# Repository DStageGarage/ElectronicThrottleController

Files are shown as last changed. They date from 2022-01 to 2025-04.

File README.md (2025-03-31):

# ElectronicThrottleController

IMPORTANT - For production in JLCPCB please use v1.3 or v2.2 files! 

This is a project of Electronic Throttle Controller also known as Drive By Wire, created by Filip from DStage garage and free to use.

## HW generation 1
> [!IMPORTANT]
> ETC v1.3 is only suited for potentiometer based throttle position sensors and gas pedals as it uses a simple calibration method.
> 
The board is purely analogue, no programming required and no chance of failure due to MCU hang-up, flash disappearing due to harsh engine environment etc. Safety was a priority with this one ;-) It also has build in simple fail safes - in case any of the control wires is broken or shorted with power for example the throttle will close automatically.

The board shape is designed to fit popular aluminium casing to be found in tme.eu, Farnell etc. You can also use the provided STL file for 3D printing the case.There are no connectors, wires are soldered directly to the board to keep it compact.

You can also check a video to learn more about this project: https://www.youtube.com/watch?v=MTnsbOgZkUA 

## HW generation 2
> [!TIP]
> ETC v2.2 is suited for all types of throttle position sensors and gas pedals as it uses a different calibration method in comparison to v1.3.

The main functionality is purely analogue. If no special functions are desired the provided place for an optional Arduino Nano may stay unpopulated, no actions are required and the board will work in the same way as generation 1. The optional module can be used to monitor sensors but also to create a gas pedal map if required (basic SW in beta version is provided). All signals connected to the Arduino are buffered to minimise the risk in case of program failure. The usage of the Arduino module for throttle control has to be delibatery selected by desoldering jumper Z1 and soldering Z2. 

Wires can be soldered directly to the board, but this version allows you to use ARK terminals (screw terminals) instead. If PCB and assembly is ordered in JLCPCB user can chose BOM file with or without ARK terminals.
Besides the different input circuitry/calibration method compared to generation 1 this one is improved and better optimised in terms of heat dissipation.

The board form factor is larger than for version 1, but it will fit a popular aluminium casing, and a STL file for 3D printing is also provided. 

Here's a quick video comparing v2.2 with v1.3 https://studio.youtube.com/video/byb1L_GXVq8/edit

# Disclaimer: 
This device is dedicated for stationary engines and vehicles driving on private closed
properties. It should not be used on public roads!

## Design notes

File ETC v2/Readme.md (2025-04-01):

# ETC v2.x - 2nd HW generation

## Hisotry of changes
Last update 2024.11.13:
> [!IMPORTANT]
> A new recomended "low gain" BOM added.
> There is a known problem with some of the throttles where they tend to "flap" at some positions or when position is changed. This is most likely caused by the high gain of the error aplifier in PWM controller. In simple terms the PWM changes very fast so the throttle motor can not keep up thus starts oscilating.
> There are documented cases where lowering the gain  solves that issue. This new BOM changes value of R7 from 10k to 1k and R8 from 1k to 2.2k, efectively changing the ęrror amplifier gain from ~10 to ~0.45. This has not been tested with a "model" Bosch throttle yet but shouldn't cause any issues.

2023.10.04:
- beta SW for Arduino Nano and PC added, not tested

2023.08.30:
- two variants of 3D models fo case added

2023.08.22:
- Alternative BOM file version for v2.2 inclused screw terminal connectors so you can order them soldered in via JLCPCB
  
## Connection
| Connector | Signal | Function |
| :---: | :---: | :--- |
| P1 | GP | Gas pedal position signal. Most cases there are two redundand outputs from the gas pedal, use one on which voltage increases with pushing the pedal further. If both outputs have inclinig signal the one with wider voltage range is usually preferable. |
| P1 | GND | Use this pin for both gas pedal and TPS ground (negative power terminal). In case of potentiometer based sensors connect it to the low side of the potentiometer. |
| P2 | +5V | Use this pin for both gas pedal and TPS power (positive power terminal). In case of potentiometer based sensors connect it to the high side of the potentiometer. |
| P2 | TH | Throttle Position Sensor signal. Most cases there are two redundand outputs from the TPS, use one on which voltage increases with openning the throttle further. If both outputs have inclinig signal the one with wider voltage range is usually preferable. |
| P3 | GND | Use this pin for connecting to ECU signal ground when using IAC input and/or sharing the TPS signal. |
| P3 | IAC | Idle air PWM signal input from the ECU. In cas ECU has an open-collector/open-drain style IAC output (only connects to ground) user has to add pull-up resistor (for example 10k) to +5V on this input. Preferably the PWM signal should be 0-5V but 0-12V will also work. Please note that IAC has relatively high range by default and can open the throttle up to 30%. R26 can be increased in value to tighten the range and improve control resolution. |
| P4 | PWR | Main power terminal. Connect to +12V with a 5A fuse and a minimum of 1mm2 wire. |
| P4 | GND | Power ground for the board. Connect to a power ground on the vehicle with a minimum 1mm2 wire. |
| P5 | M1 | Throttle motor terminal 1. Polarity has to be checked experimentaly. |
| P5 | M2 | Throttle motor terminal 2. Polarity has to be checked experimentaly. |

## Calibration
Please refer to the DStage_ETC_v2.2_calibration.xlsx spreadsheet for calibration instructions.

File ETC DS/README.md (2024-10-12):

# DStage ETC DS
The "DS" stands for DSpeed as this version of ETC is dedicated for the Speeduino ECU by DStage called DSpeed: https://github.com/DStageGarage/DSpeed
It is based on HW version 2 howere it lacks the optional Arduino Nano module - as it is installed directly in the ECU some users can connect directly to ECU pins to creat gas pedal map if desired.

> [!IMPORTANT]
> Please note that this is a new project and has not yet been tested. It contains some crucial changes over ETCv2 such as the H-brdgethe being an integrated circuit intead of individual components. ALso the Layout is significantly different. Therefore there's no way of telling if it will behave as expected at the moment.

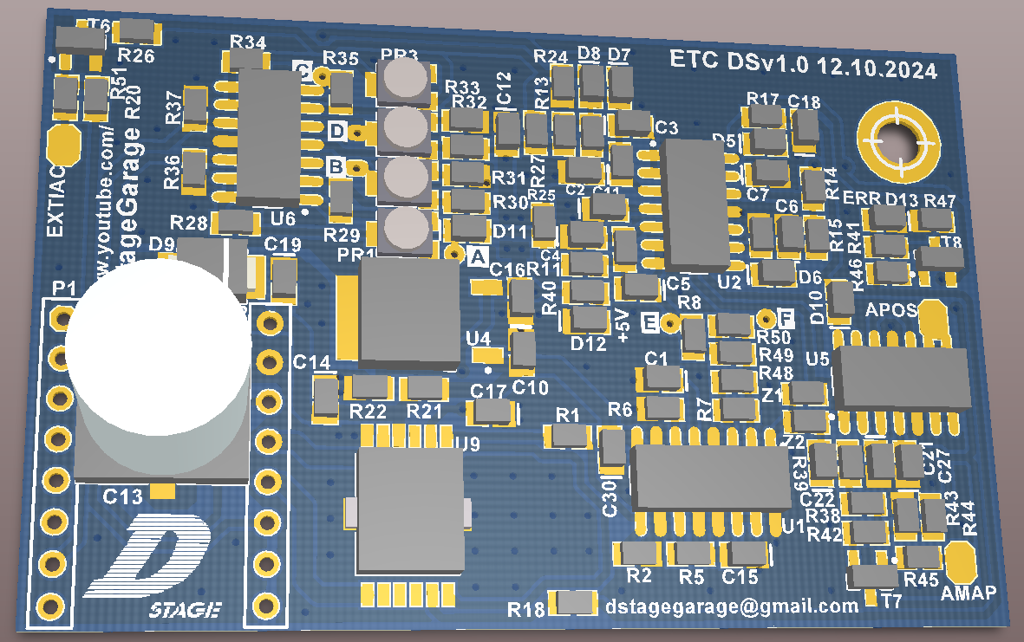
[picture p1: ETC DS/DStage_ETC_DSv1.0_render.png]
Render


For calibration instructions please use same sheet as for DSTage_ETCv2.2 - [DStage_ETC_v2.2_calibration.xlsx](https://github.com/DStageGarage/ElectronicThrottleController/blob/main/ETC%20v2/v2.2/DStage_ETC_v2.2_calibration.xlsx).

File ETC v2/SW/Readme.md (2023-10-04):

# SW for ETC v2.x

ETC v2.x allows for an optional Arduino Nano module. You will find the firmware for Arduino in "Arduino" folder and the aplication for controling it via PC in the "PC app" folder. 

Last update 2023.10.04:
- First beta version of both FW and app added. Please note that saving gas pedal map to a file as well as loading from a file is not yet available. Reading settings from Arduino to PC is slow and may be unstable when read multiple times so please pay attention if data makes sense. SW was not fully tested in real life conditions. Using Arduino functionality requires removing Z1 and adding Z2 jumper on the PCB. At the moment the Arduino code is fixed for "2000 RPM" which means it won't differentiate the map between RPMs and it's best to keep all columns in tyhe pam the same and set one of them to 2000 RPM. This can be easily incommented in the code and RPM signal can be used. For that user has to provide RPM signal from ECU to pin D3 of the Arduino Nano module - there is an extra pad on the v2.2 PCB next to that pin but no ARK connector. Signal cannot exceed 5V!

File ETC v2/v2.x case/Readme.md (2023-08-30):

# 3D model for ETC v2.x case

## DStage ETC basic case
Here you can find the basic project of 3d printable case for ETC v2.x PCB in Fusion 360 format.

There are also a ready to use stl models. Please note that the basic models do not contain holes for wires so user has to chose location for those and drill them manually. 
Models including wholes and mounting tabs will be added in future.

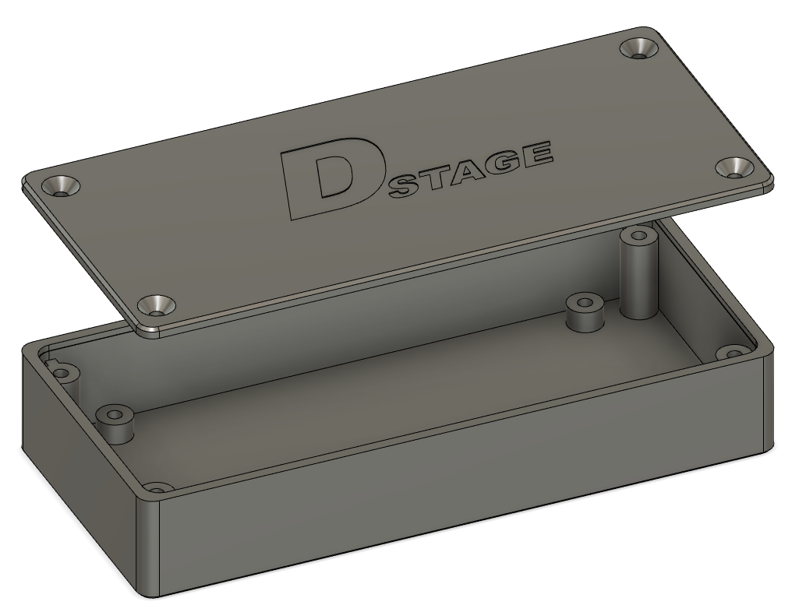
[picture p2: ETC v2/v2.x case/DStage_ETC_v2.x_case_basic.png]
Basic model for ETC v2.x without holes and tabs


## Alternative case by RSMtuning
Another approach to the case designed by one of the users - RSMtuning. This one does not use short bolts for PCB holding but a build in plastic spacer.

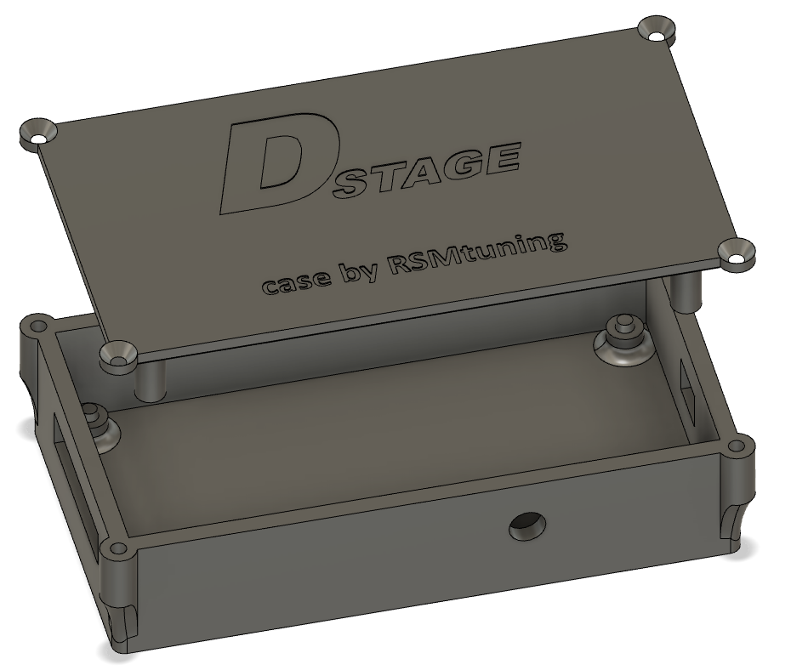
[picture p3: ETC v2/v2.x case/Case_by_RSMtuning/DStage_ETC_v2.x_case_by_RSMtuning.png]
Model for ETC v2.x by RSMtuning


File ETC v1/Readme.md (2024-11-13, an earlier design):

# ETC v1.x is the first HW generation 

2024.11.13:
> [!IMPORTANT]
> A new recomended "low gain" BOM added.
> There is a known problem with some of the throttles where they tend to "flap" at some positions or when position is changed. This is most likely caused by the high gain of the error aplifier in PWM controller. In simple terms the PWM changes very fast so the throttle motor can not keep up thus starts oscilating.
> There are documented cases where lowering the gain  solves that issue. This new BOM changes value of R7 from 10k to 1k and R8 from 1k to 2.2k, efectively changing the ęrror amplifier gain from ~10 to ~0.45. This has not been tested with a "model" Bosch throttle yet but shouldn't cause any issues.

2023.09.06:
- added 3D model for printing a case for v1.x

2023.03.26:
- v1.3 - changed the frequency of TPS input filter from 150Hz to 720Hz to avoid problem of tgrottle "flapping" due to too slow response presumably. 
  The new value has been tested on the bench and seems to solve the issue. No needto remove C2 and C3 now. 
  Changed component values: R9 from 5k1 to 10k, C2 from 100n to 22n, C3 from 220n to 22n.
- v1.3 - changed throttle motor PWM frequency from quite high ~300kHz to resonable ~100kHz. This change vastly reduces heat loss in H-bridge MOSFET transistors.
  As the dead time is achieved by difference in time of openning and closing the transistors (open by resistor, close by diode) majority of heat loses
  comes from channel opening time. With reduced frequency transistors are now much cooler.
- v1.3 - updated schematic in user manual and added note that there may be small differences in the looks of JLCPCB component list due to above changes in BOM.

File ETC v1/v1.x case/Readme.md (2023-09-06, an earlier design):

# 3D model for ETC v1.x case

Here you can find the basic project of 3d printable case for ETC v1.x PCB in Fusion 360 format.

There are also a ready to use stl models. Please note that the basic models do not contain holes for wires so user has to chose location for those and drill them manually. 
Models including wholes and mounting tabs may be added in future.

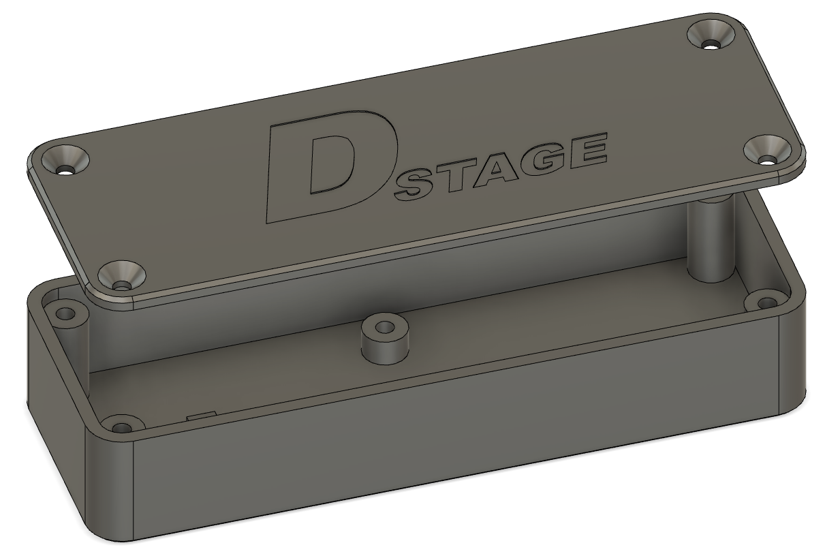
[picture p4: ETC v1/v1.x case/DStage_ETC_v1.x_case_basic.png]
Basic model for ETC v1.x without holes and tabs


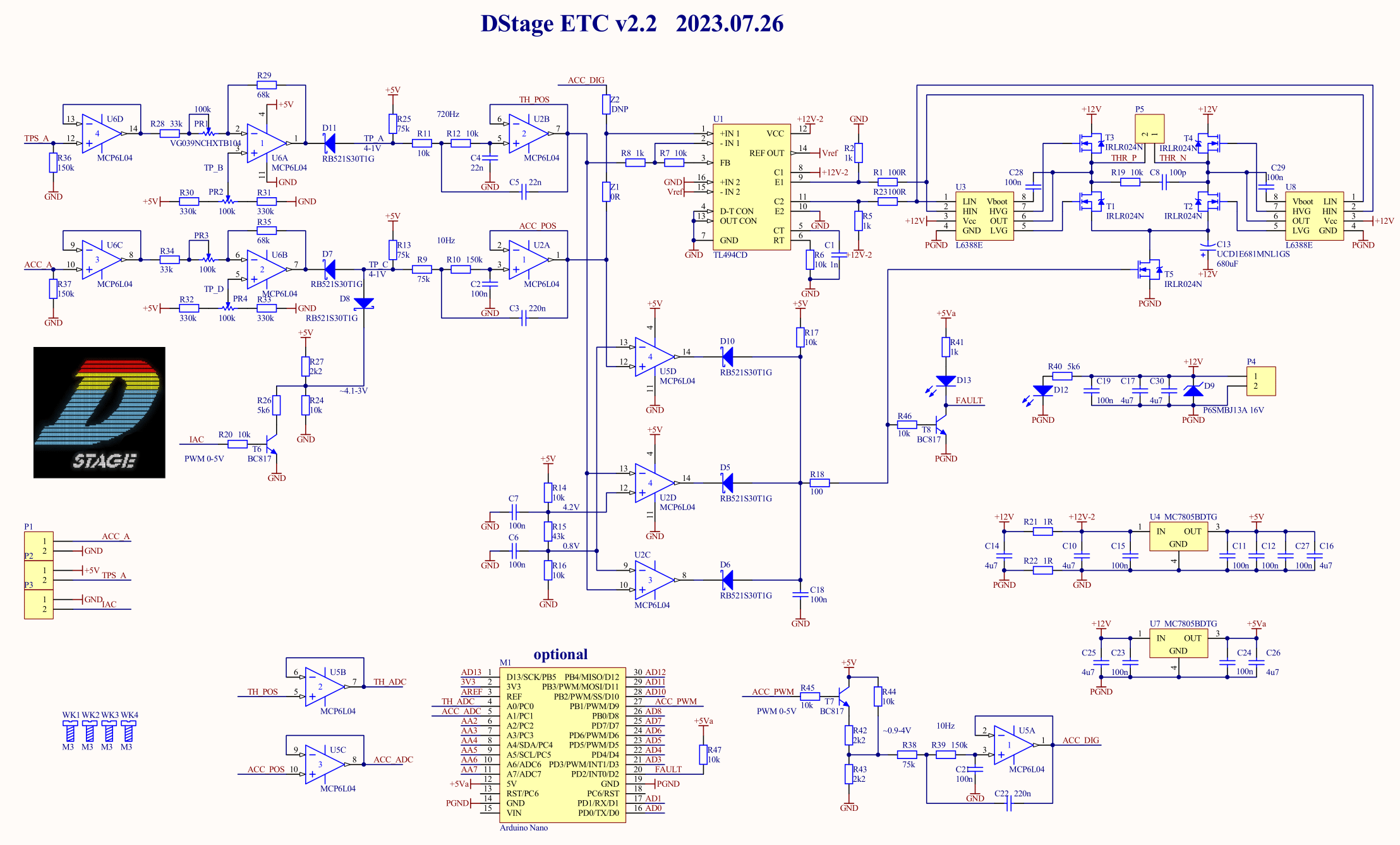
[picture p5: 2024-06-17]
ETC v2/v2.2/DStage_ETC_v2.2_schematic.png

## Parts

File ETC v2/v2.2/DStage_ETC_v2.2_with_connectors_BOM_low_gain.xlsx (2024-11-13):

Comment | Designator | Footprint | JLCPCB part #
RB521S30T1G | D5-8,D10-11 | 0805 | C167133
P6SMBJ13A | D9 | SMB | C86366
LED GREEN | D12 | 0805 | C2297 | basic
LED RED | D13 | 0805 | C84256 | basic
IRLR024N | T1-5 | D-Pak | C3007
S8050 | T6-8 | SOT-23 | C2146 | basic
TL494CD | U1 | SO16 | C19882 | extd
MCP6L04 | U2,U5-6 | SO14 | C116668
L6388E | U3,U8 | SO8 | C23921 | extd
MC7805BDTG | U4,U7 | D-Pak | C83632 | extd
100Ω | R1,R18,R23 | R0805 | C17408 | basic
1kΩ | R2,R5,R41 | R0805 | C17513 | basic
5.6k | R40,R26 | R0805 | C4382 | basic
10k | R6,R8,R11-12,R14,R16-17,R19-20,R24,R44-47 | R0805 | C17414 | basic
75k | R9,R13,R25,R38 | R0805 | C17819 | basic
150k | R10,R36-37,R39 | R0805 | C17470 | basic
330k | R30-33 | R0805 | C17629 | basic
43k | R15 | R0805 | C17695 | basic
1R | R21-22 | R0805 | C25271 | basic
2.2k | R7,R27,R42-43 | R0805 | C17520 | basic
68k | R29,R35 | R0805 | C17801 | basic
33k | R28,R34 | R0805 | C17633
100k | PR1-4 | SMD-3_3.0x3.8x1.2 | C128545 | extd
0Ω | Z1 | R0805 | C17477 | basic
1nF | C1 | C0805 | C46653 | basic
100nF | C2,C6-7,C11-12,C15,C18-19,C21,C23-24,C27-29 | C0805 | C28233 | basic
220nF | C3,C22 | C0805 | C5378 | basic
100pF | C8 | C0805 | C1790 | basic
270uF | C13 | SMD-ECAP-10x10 | C311670 | extd
4.7uF | C10,C14,C16-17,C25-26,C30 | C0805 | C1779 | basic
22nF | C4-5 | C0805 | C1729
screw terminal | P1-5 | 5mm | C474881 | extd

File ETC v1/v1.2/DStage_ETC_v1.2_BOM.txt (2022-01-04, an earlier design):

BOM for ETC project is shared via Google Drive for ease of use in Google spreadsheets. 

# Please follow this link: 
https://docs.google.com/spreadsheets/d/1jGTcMW5XZCuBMflX-EJ1iahN-_moxMeDLij978g0fmc/edit?usp=sharing 

The sheet inlused details regarding all components and their replacement as well as a tab with format dedicated for automatic assembly in JLCPCB.

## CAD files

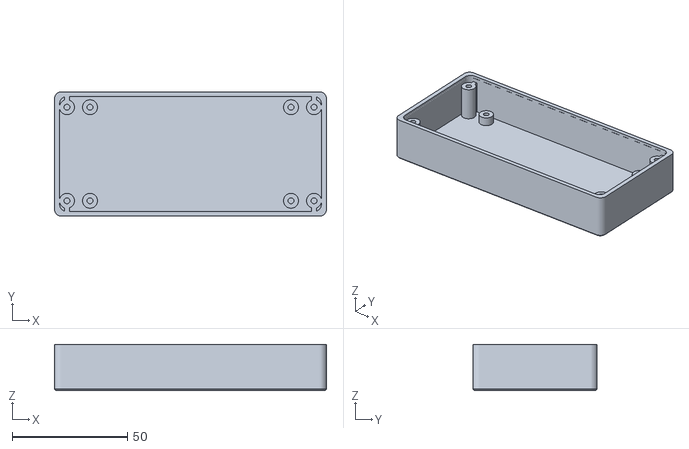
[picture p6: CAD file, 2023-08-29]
ETC v2/v2.x case/DStage ETC v2.x case main no holes.stl
118.0 x 54.0 x 20.0

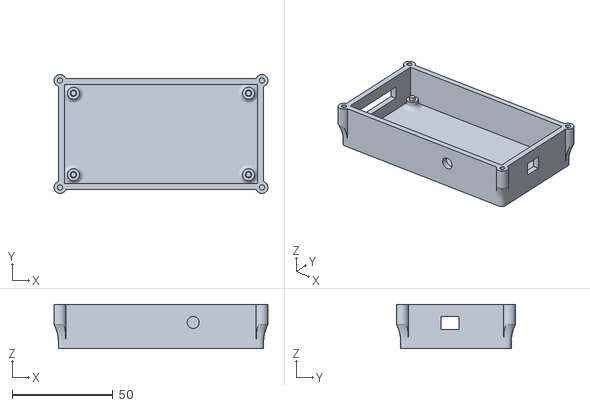
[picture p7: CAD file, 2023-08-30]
ETC v2/v2.x case/Case_by_RSMtuning/DStage_ETC_v2.x_case_by_RSMtuning_main.stl
106.3 x 59.1 x 22.0

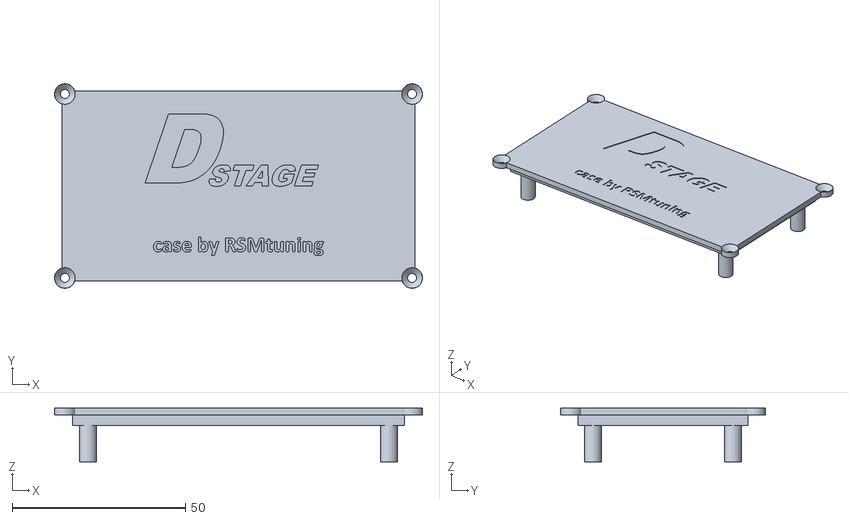
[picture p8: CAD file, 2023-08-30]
ETC v2/v2.x case/Case_by_RSMtuning/DStage_ETC_v2.x_case_by_RSMtuning_lid.stl
106.3 x 59.1 x 15.5

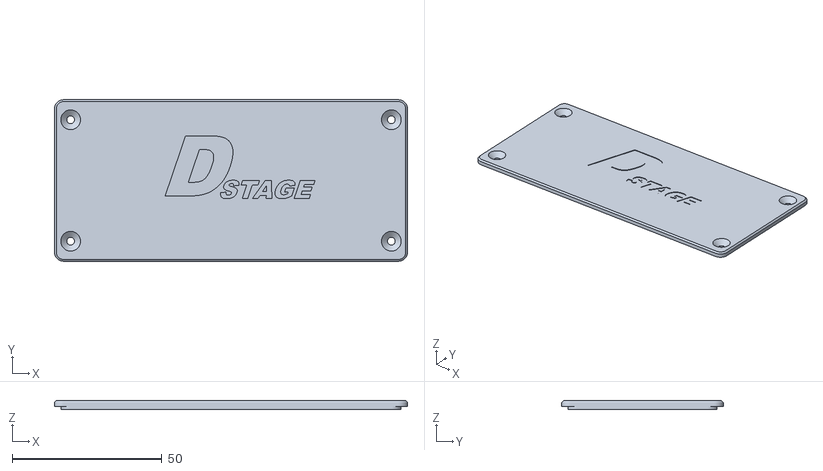
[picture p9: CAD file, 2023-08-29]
ETC v2/v2.x case/DStage ETC v2.x case lid no holes.stl
118.0 x 54.0 x 3.00

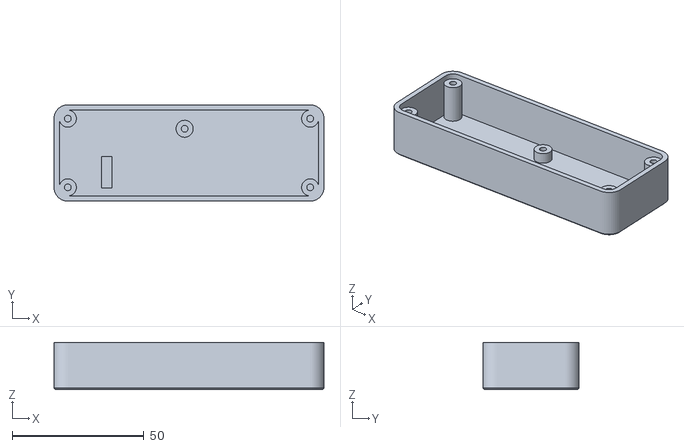
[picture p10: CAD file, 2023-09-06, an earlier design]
ETC v1/v1.x case/DStage ETC v1.x case main no holes.stl
102.5 x 36.6 x 18.0

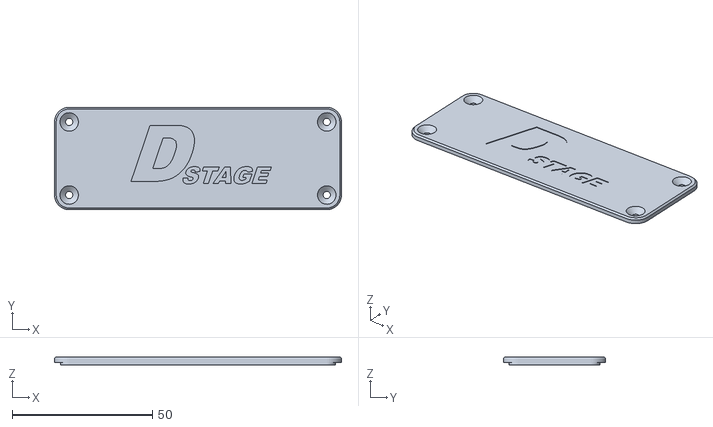
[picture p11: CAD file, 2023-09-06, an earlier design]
ETC v1/v1.x case/DStage ETC v1.x case lid no holes.stl
102.5 x 36.6 x 3.00

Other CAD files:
ETC v1/v1.x case/DStage ETC v1.x case basic project.f3d
ETC v2/v2.x case/Case_by_RSMtuning/DStage_ETC_v2.x_case_by_RSMtuning.f3d
ETC v2/v2.x case/DStage ETC v2.x case basic project.f3d

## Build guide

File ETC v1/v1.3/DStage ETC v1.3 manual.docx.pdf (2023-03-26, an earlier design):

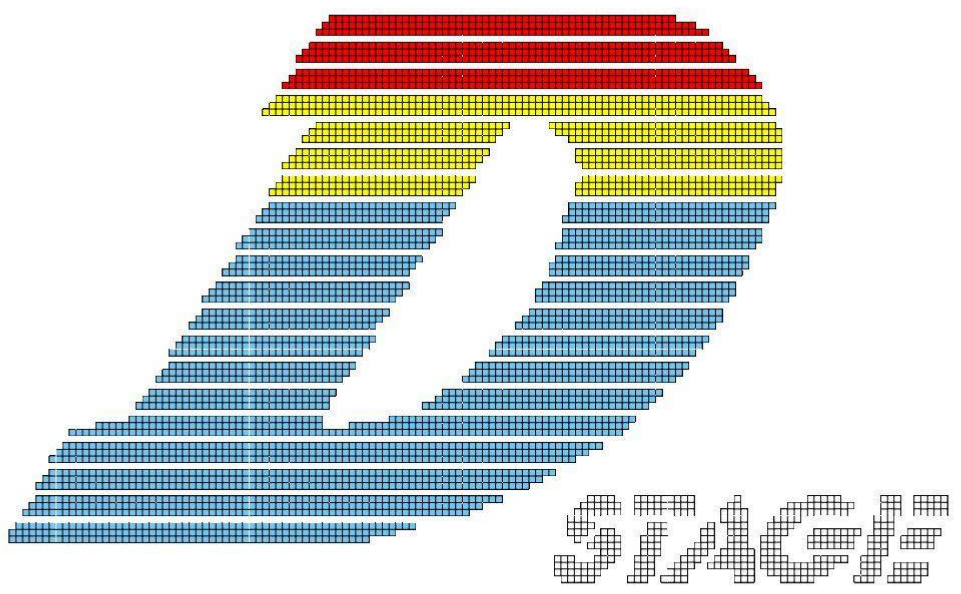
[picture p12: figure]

# Electronic Throttle Controller

a.k.a.

# Drive by Wire

# ETC v1.3

1

1. Introduction

The ETC v1.3 is an open project of a controller for electronic throttle for internal combustion engines. It allows control of the throttle by electronic gas pedal (accelerator) which is sometimes referred to as „drive by wire”. These are some of the features:
- Controls a DC motor based electronic throttle with H-bridge allowing for fast movement in both directions and closing the throttle beyond stationary position,
- Works with gas pedal incorporating potentiometers or voltage based output, highly adjustable input levels,
- IAC input allowing for ECU idle control with 5V PWM signal,
- Build in fail-safes for detecting broken connections or short circuits on wires connecting gas pedal and TPS,
- analogue circuit – no programming required, no risk of program failure, no risk of CPU going into race condition or resetting due to electromagnetic noise in hursh near-engine environment,
- PCB designed for enhancing immunity to noise.

DISCLAIMER:
This device is dedicated for stationary engines and vehicles driving on private closed properties. It should not be used on public roads!
2. Principle of operation

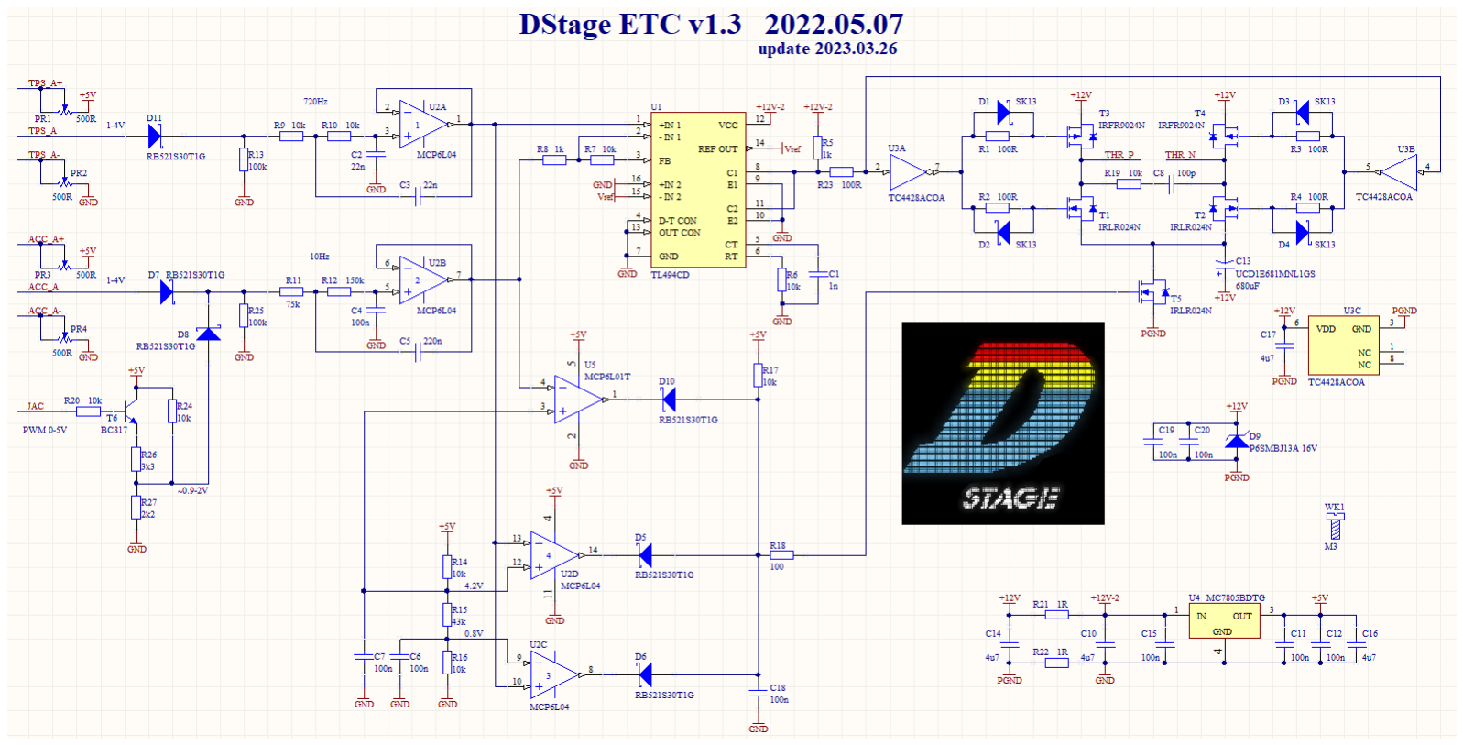
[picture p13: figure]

T.B.D.

2 Last update 2023.03.26

3. Assembly / Ordering

3.1 Automated assembly via JLCPCB

Automated assembly ordered in JLCPCB is by far the easiest option to get the controller in your hands. To order your PCBs together with components and assembly you will need to visit project repository site at https://github.com/DStageGarage/ElectronicThrottleController and download 3 files:

- DStage_ETC_v1.3_gerbers.rar - gerber files for all necessary PCB layers and drilling
- DStage_ETC_v1.3_BOM.xlsx - bill of materials in JLCPCB compatible format
- DStage_ETC_v1.3_PnP.csv - pick and place file also referred to as CPL

Then you can log into your account at JLCPCB and start the ordering process during which you will be asked for the above files (gerbers, bill of materials, pick and place file). Here’s a detailed description of that process:

- upload gerbers on the first page of the ordering process by clicking on the button (1), then select file “DStage_ETC_v1.3_gerbers.rar” (2) and click “Open” (3).

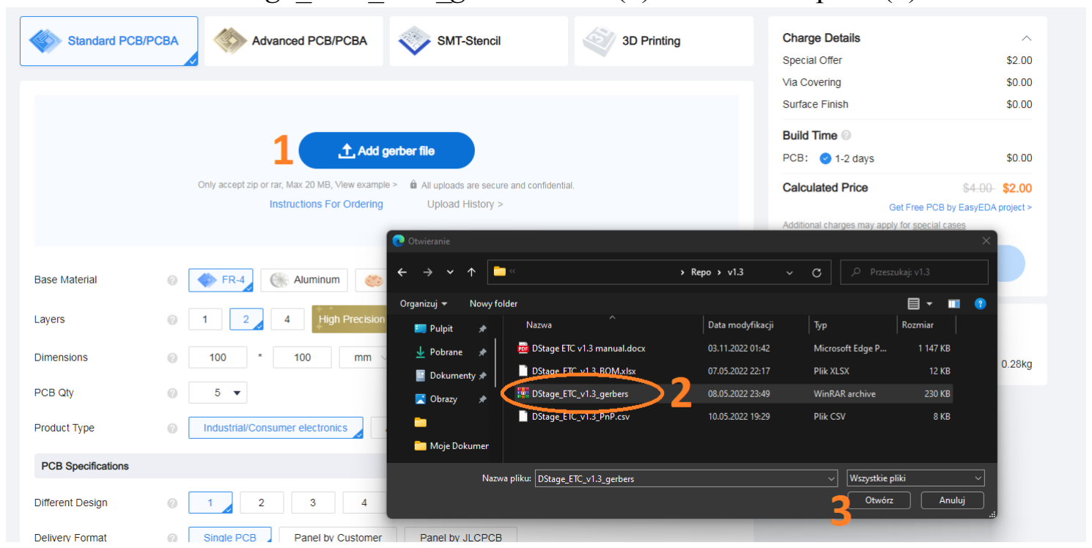
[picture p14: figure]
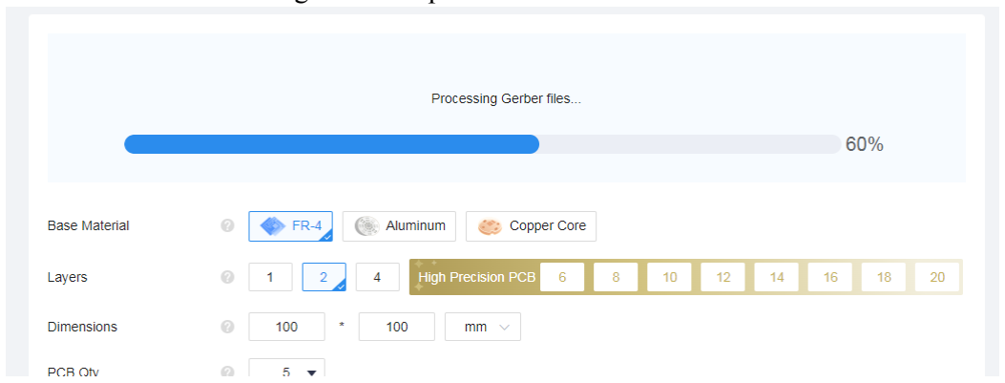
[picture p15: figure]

- wait a short while for the gerbers to upload

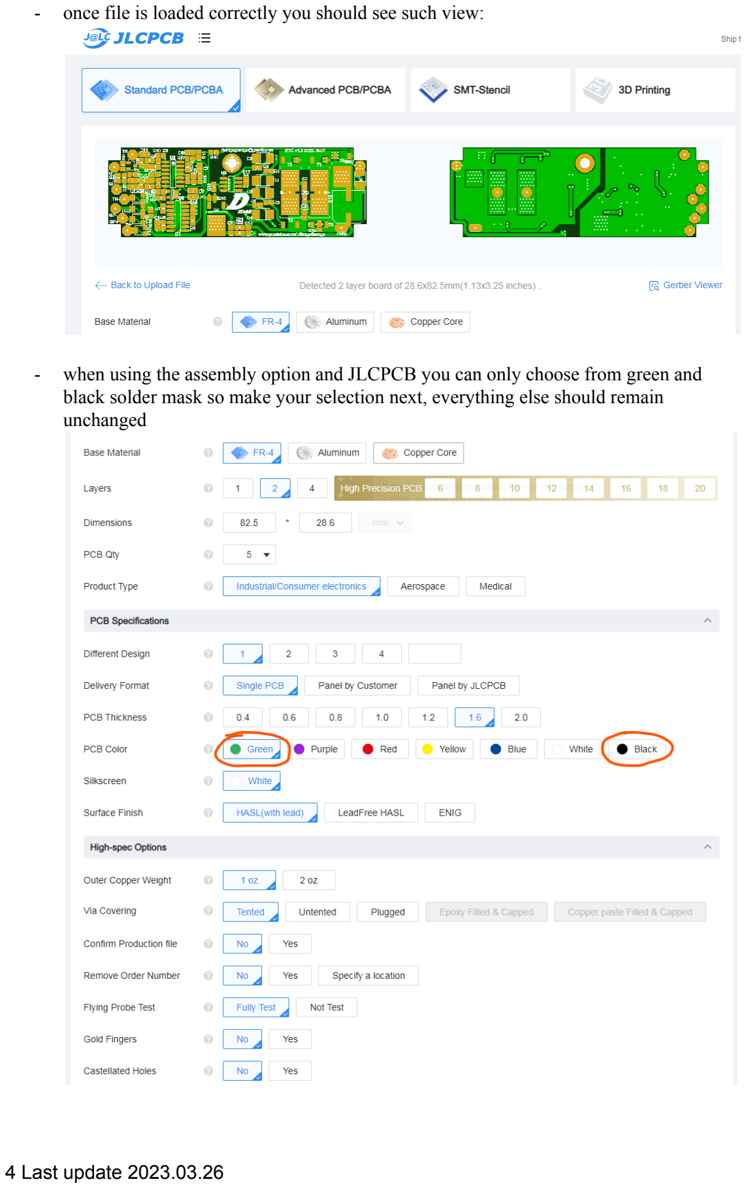
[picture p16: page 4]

- once file is loaded correctly you should see such view:
- when using the assembly option and JLCPCB you can only choose from green and black solder mask so make your selection next, everything else should remain unchanged

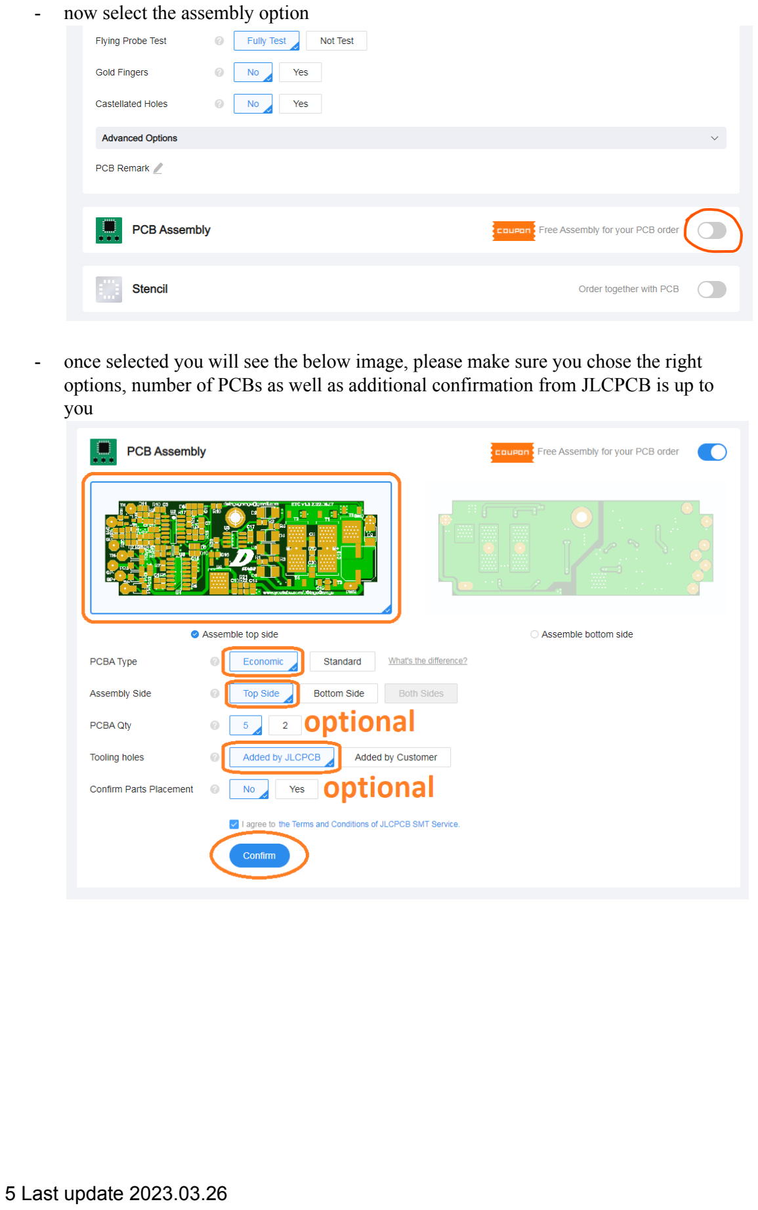
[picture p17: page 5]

- now select the assembly option
- once selected you will see the below image, please make sure you chose the right options, number of PCBs as well as additional confirmation from JLCPCB is up to you

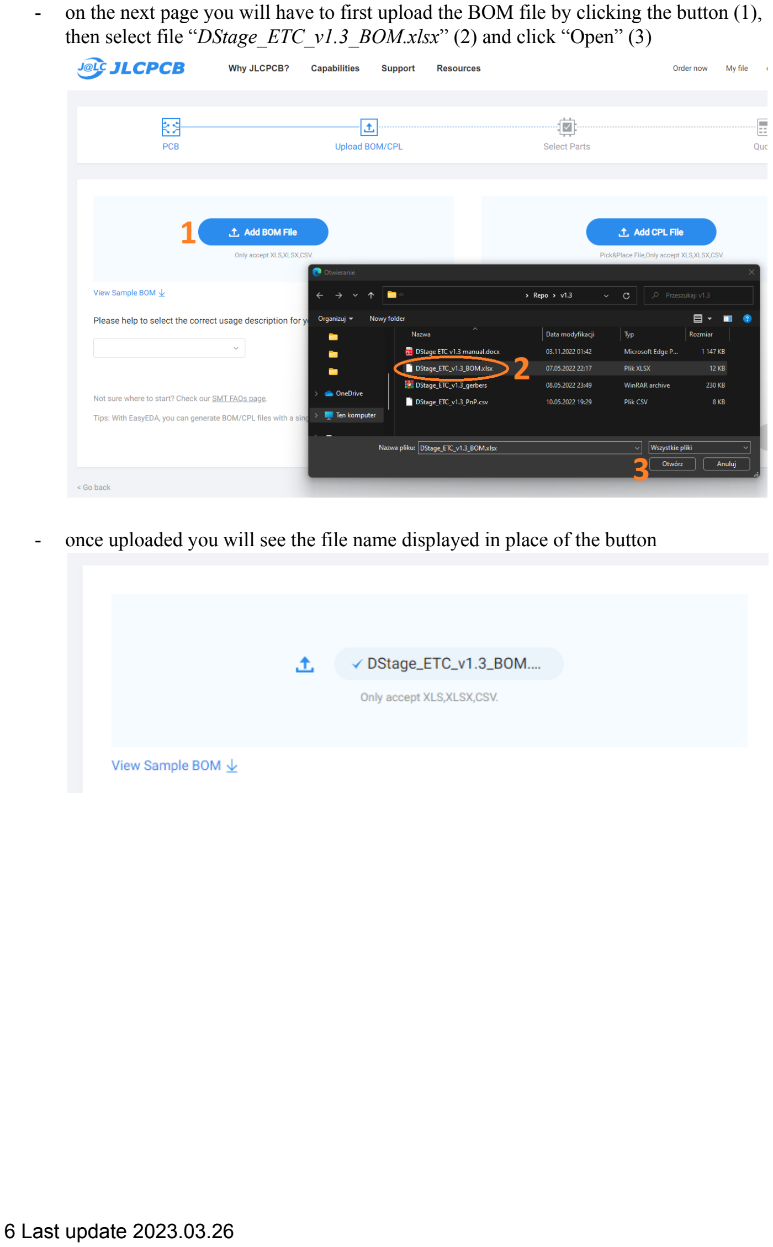
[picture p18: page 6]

- on the next page you will have to first upload the BOM file by clicking the button (1), then select file “DStage_ETC_v1.3_BOM.xlsx” (2) and click “Open” (3)
- once uploaded you will see the file name displayed in place of the button

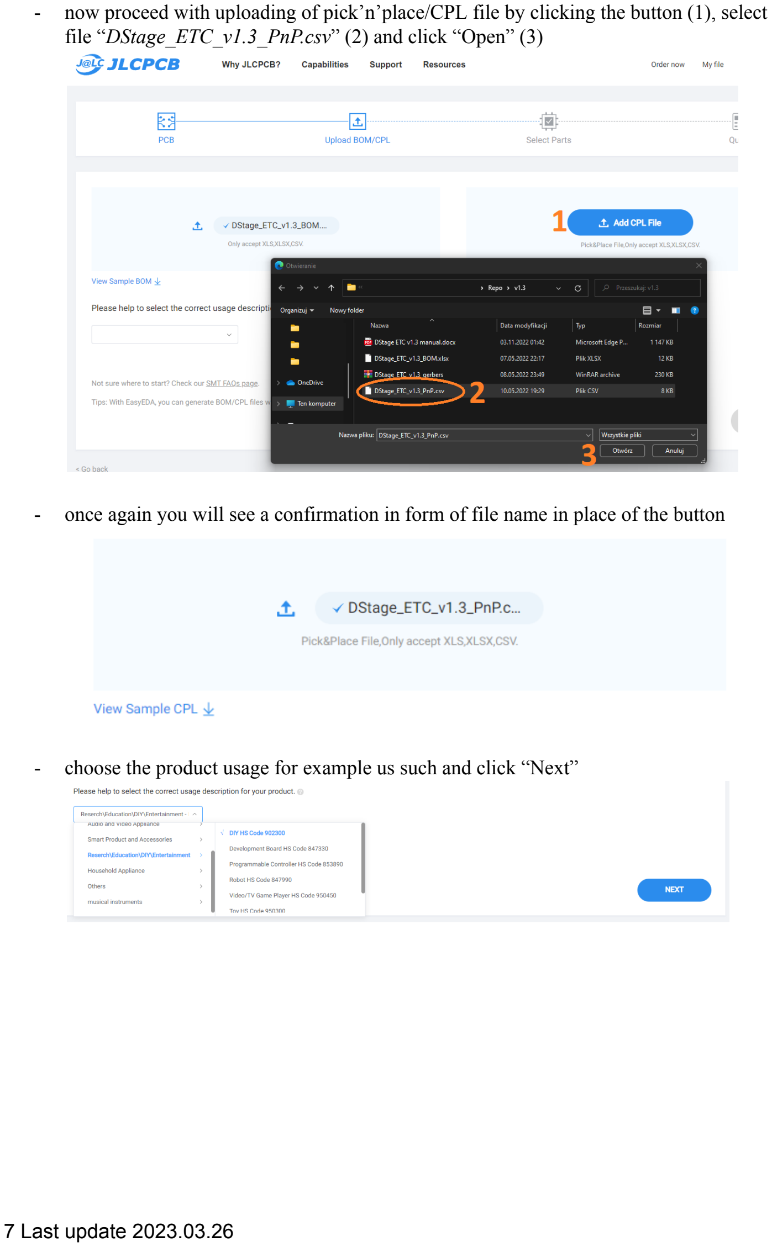
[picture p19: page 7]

- now proceed with uploading of pick’n’place/CPL file by clicking the button (1), select file “DStage_ETC_v1.3_PnP.csv” (2) and click “Open” (3)
- once again you will see a confirmation in form of file name in place of the button
- choose the product usage for example us such and click “Next”

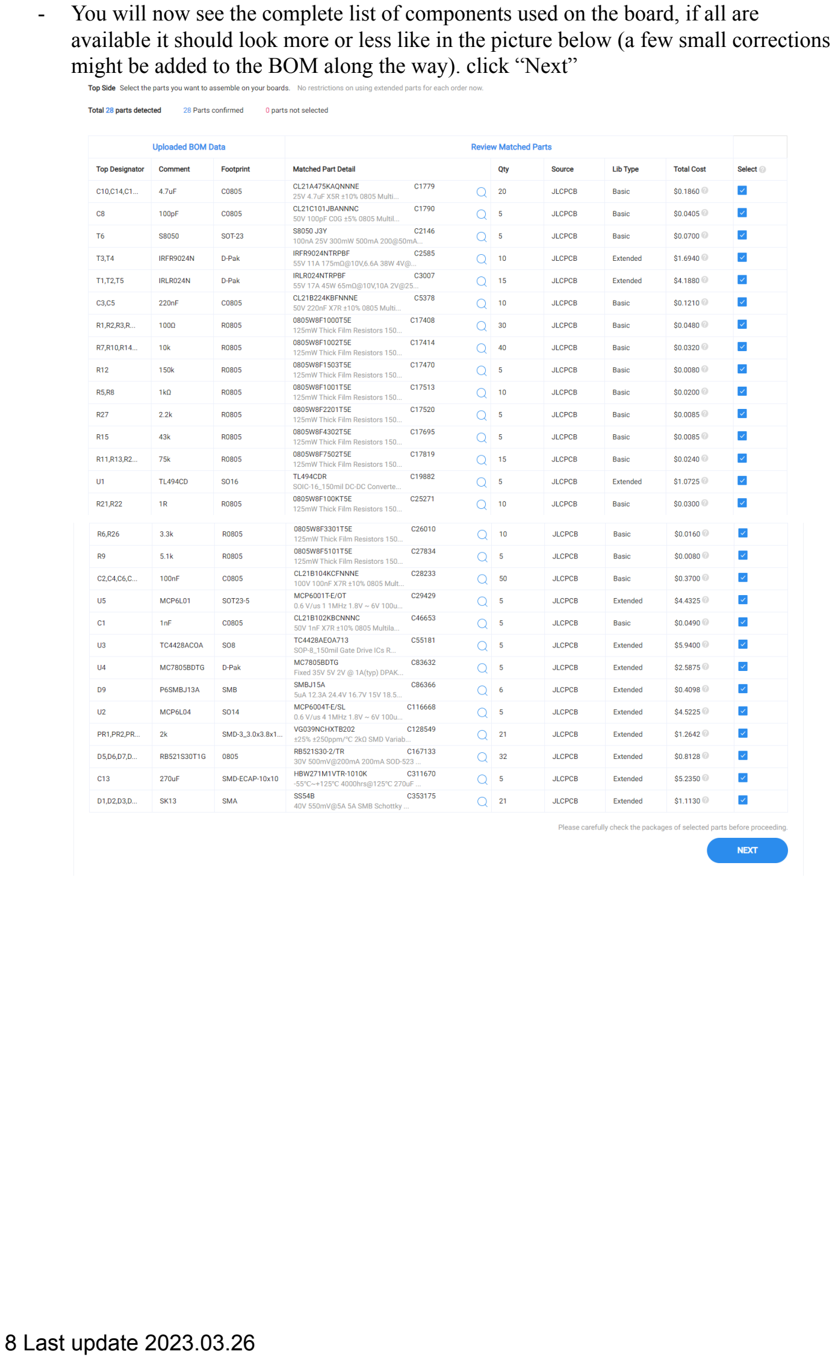
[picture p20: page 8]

- You will now see the complete list of components used on the board, if all are available it should look more or less like in the picture below (a few small corrections might be added to the BOM along the way). click “Next”

- after a short while you will be shown a picture of PCB with components, you do not have to worry about some of them being rotated the wrong way, it will be corrected by JLCPCB engineer later, just make sure that everything is there and you can finish the ordering proces by clicking “Save To Cart”

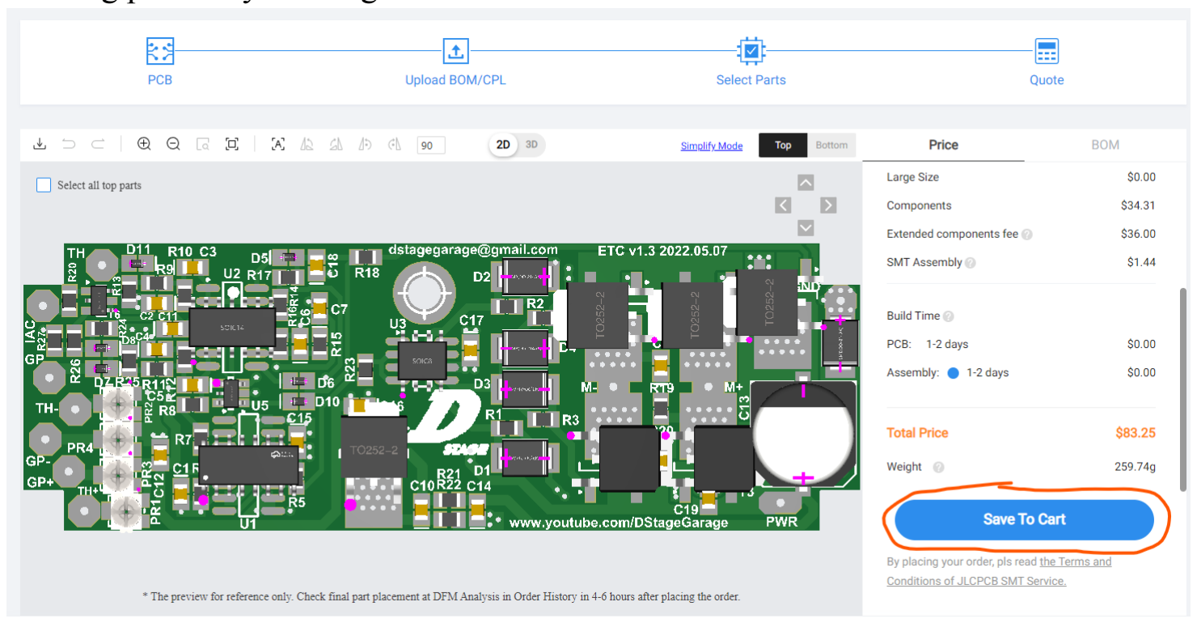
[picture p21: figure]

Please note that JLCPCB is not related to the ETC project in any way. It is just mentioned here as they provide an easy and convenient way of ordering printed circuit boards with assembly.
In case of issues such as component shortages or file problems please contact us at dstagegarage@gmail.com for help.

3.2 Manual assembly

The figure 3.1 shows the ETC v1.1 PCB view (v1.3 is nearly identical in component placement) with extra designators overlayed for clarity. All components are surface mounted on the top layer only.

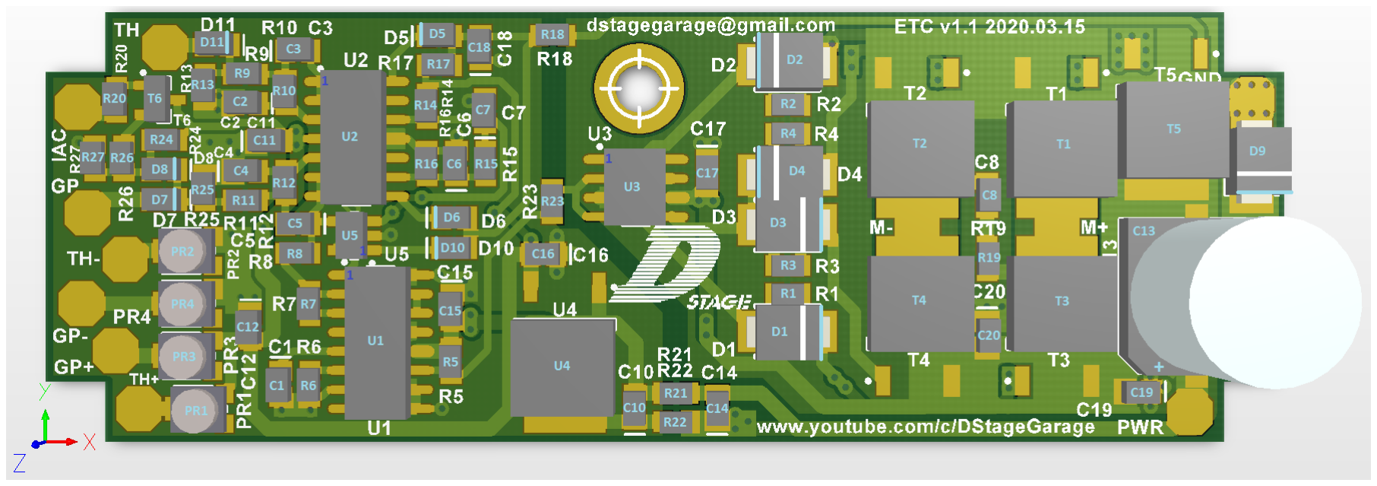
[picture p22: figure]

Figure 3.1 PCB assembly

For ease of assembly it is recommended to start with integrated circuits paying attention to correct positioning of pin #1. On SO cases (U1, U2, U3) there are
a few different ways to mark this pin.

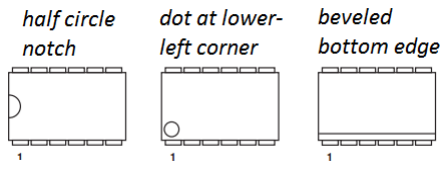
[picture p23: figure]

Figure 3.2 How to recognize pin #1 on ICs

There can be a notch on the left side, printed or molded dot in the left bottom corner or beveled bottom side. Refer to figure 3.2 for hints. On PCB silkscreen there is a dot marking where pin #1 should be. You can also check figure 3.1 for clarity. Positioning of U5 is easy as it has 2 pins on one side and 3 on the other.

Assembly can be followed-up by small passive components i.e. resistors and ceramic capacitors as well as diodes and T6 transistor. Resistors and ceramic capacitors are non polarized components so it does not matter how you orient them on pads (line to the side of capacitors footprints is only there to easier distinguish them from resistors). In case of diodes it is important to match the bar on case with the bar/line printed on silksreen. Please refer to figure 3.1. Positioning of T6 is self explanatory (1 pin on one side, 2 on the other).

Now the assembly can be finished by populating potentiometers, bigger transistors T1-T5 and electrolytic capacitor C13 as the last component as it’s the largest one. Such capacitors are polarized so it is important to place them in the correct way. It usually has a black bar at the negative side (-) and notched corners at the base on the positive side (+). Please check figure 3.1 for clarity.

4. Wiring (connecting to the vehicle/engine/ECU)

To keep PCB compact there are no connectors. Instead all wiring is done via direct soldering of wires to 11 pads. Figure 4.1 shows the layout of those pads and wires for particular functions.
On the right side there are two power pads – ground at the top and 12V power at the bottom. Please make sure that the power is fed with a fuse not larger than 5A to ensure safe operation in case of the throttle motor failure etc.
The motor of the electronic throttle is connected to pads located very close to H-bridge. Please note that in ETC v1.1 the M+ and M- pad markings will be most likely reversed for most types of electronic throttles. Figure 4.1 already shows that the polarity should be reversed. The markings on later versions of PCB have been corrected.
On the left hand side there are 7 pads in total. The one marked as IAC should be connected to the ECU idle PWM signal.

The group of 3 pads marked GP, GP+ and GP- is meant for connecting the gas pedal (accelerator). Usually electronic gas pedals have 6 pins, 3 for one potentiometer or circuit imitating the potentiometer and 3 for another one. Those two outputs depending on a particular type of gas pedal can be configured in different manner. The output signal can have different offset, direction or characteristics (slope, especially in models using voltage output instead of true potentiometers). What is important is to make sure the output used with ETC has the voltage increasing when the pedal is pushed (pot slider going towards positive side) and decreasing when released (pot slider going towards negative side). More on different accelerator types in one of the following chapters.
The last group of 3 pads is dedicated to the feedback position of the throttle. Usually electronic throttles use double potentiometer with combined ends and separate outputs which results in 4 pins being used for that purpose. Typically one potentiometer travels one direction and the second one in the opposite direction with throttle movement. Again, make sure to use the output that increases the voltage (pot slider traveling towards the positive side) when the throttle is opened more. This can be checked by measuring resistance change across the pins while manually moving the throttle. More on that in one of the following chapters.

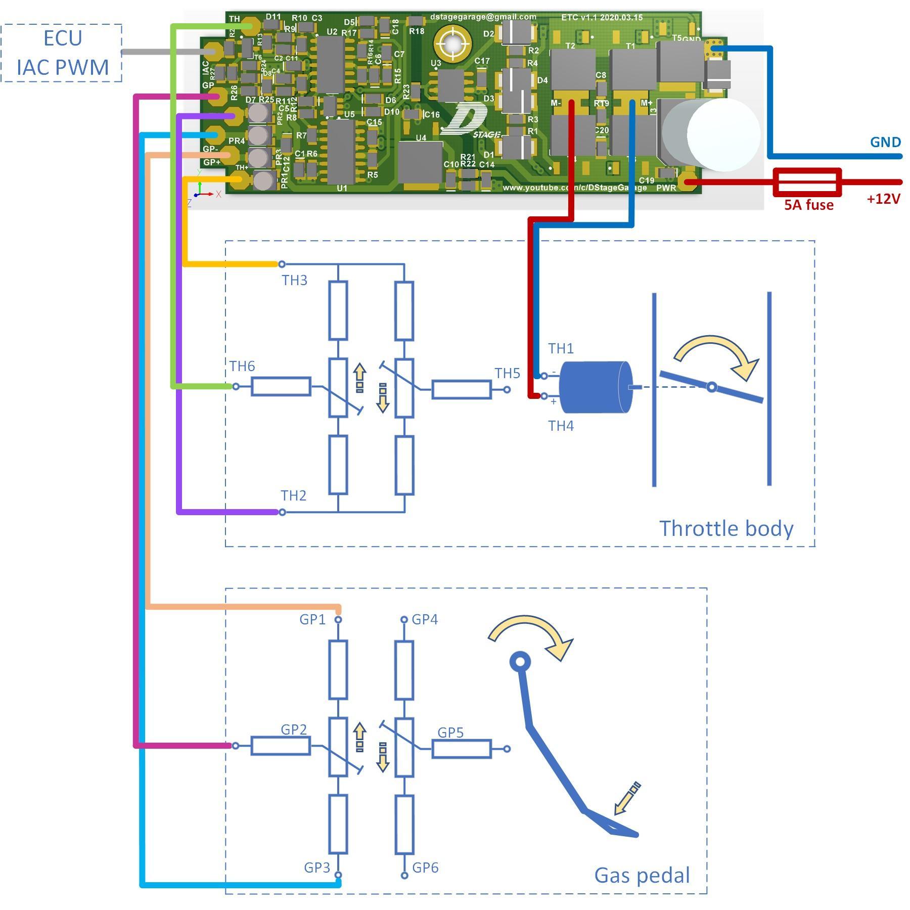
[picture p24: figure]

Figure 4.1 Wiring diagram
5. Calibration
We start with the throttle position sensing:
1. Connect the TH, TH+ and TH- to the throttle but DO NOT yet connect the motor (M+ and M-).
2. With throttle closed measure the voltage at TH and adjust PR2 so the voltage is close to 1V (doesn't have to be spot on as long it is reasonably higher than 0.8V).
3. Now fully open the throttle manually and check the voltage on TH. Then adjust PR1 so the voltage is close to 4V (doesn't have to be spot on as long it is reasonably lower than 4.2V).

4. Close the throttle and repeat point number 2 and then number 3 a few times until voltage on TH is close to 1V with the throttle closed and 4V with the throttle open without further touching of the pots.

Now the gas pedal/accelerator - basically same procedure:

1. Connect the GP, GP+ and GP- to one of the gas pedal potentiometers.
2. With the gas pedal unpressed measure the voltage at GP and adjust PR4 so the voltage is close to 1V (doesn't have to be spot on as long it is reasonably higher than 0.8V).
3. Now press the gas pedal and check the voltage on GP. Then adjust PR3 so the voltage is close to 4V (doesn't have to be spot on as long it is reasonably lower than 4.2V).
4. De-press the gas pedal and repeat point number 2 and then number 3 a few times until voltage on GP is close to 1V with the pedal unpressed and 4V with the pedal fully pressed without further touching of the pots.Ideally those voltages should be closely matching those measured at the end of TPS calibration procedure.

Now you can connect the M+ and M- and fingers crossed it should work.
In case of issues please contact us for help at dstagegarage@gmail.com.
6. Different gas pedal (accelerator) types and how to use them T.B.D.
7. Basic multimeter measurements.
T.B.D.

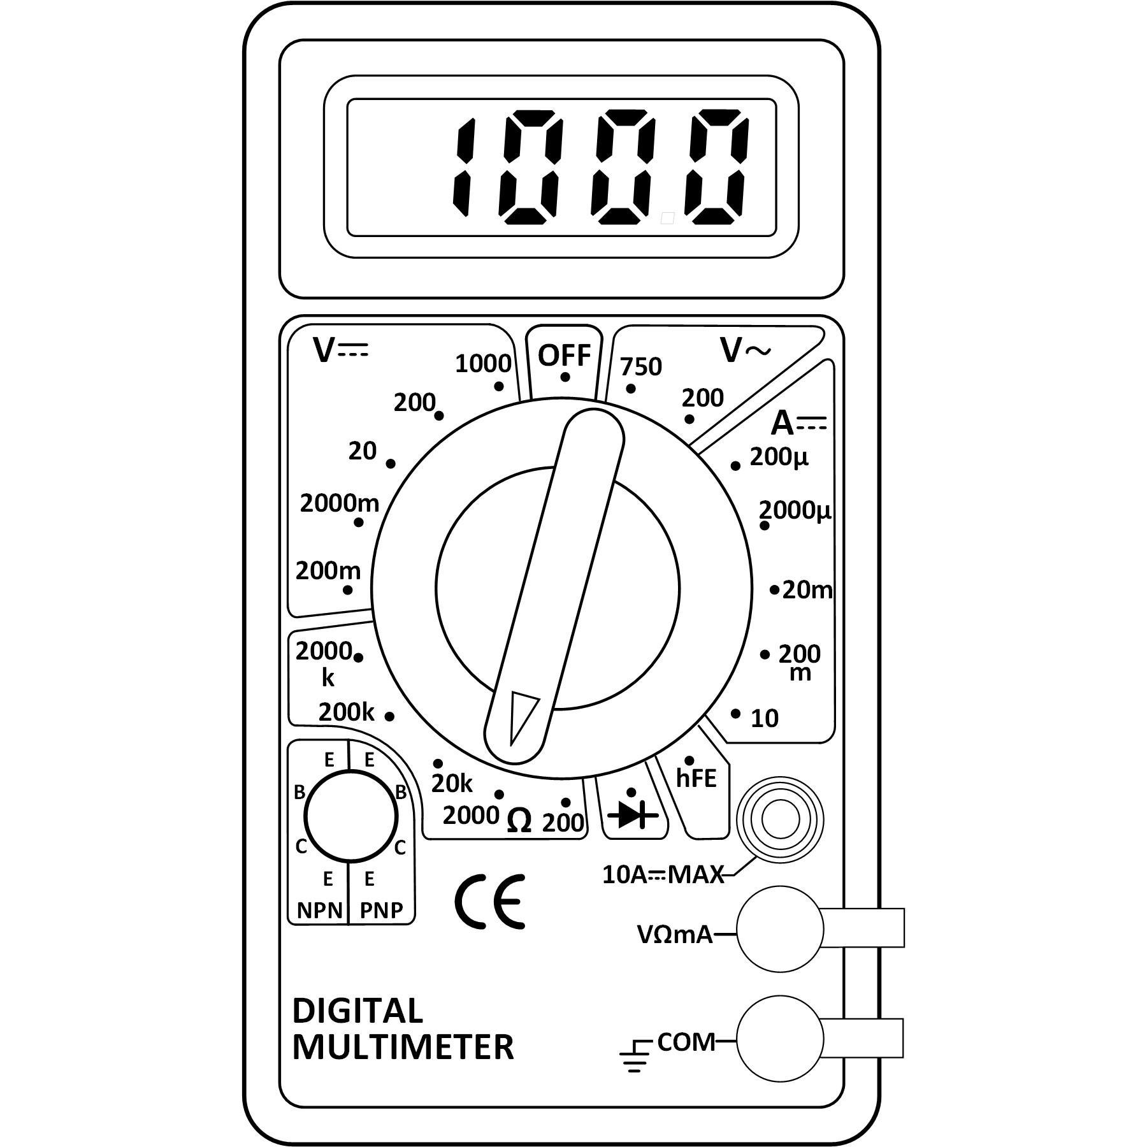
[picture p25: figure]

8. History of changes.
Date | By | Changes
2022.01.05 | DStage | Spelling checked ;-)
2022.05.08 | DStage | automated assembly chapter, calibration
2022.11.03 | DStage | minor corrections and clarifications
2022.12.13 | DStage | detailed description of JLCPCB ordering process

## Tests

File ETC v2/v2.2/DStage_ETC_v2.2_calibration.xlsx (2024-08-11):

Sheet: Calculations
 |  |  |  |  | Calibration should be performed with throttle motor disconnected!
Throttle |  |  | value type | info
Throttle sensor voltage when fully closed | 0.885 | V | input | Step 1 | Calibration procedure to get you in the ball park:
Throttle sensor voltage when fully oppened | 4.75 | V | input | Step 2 | Step 0 - connect the throttle and gas pedal inputs and power to the board (power meaning +5V and GND).
 |  |  |  |  | Step 1 - Keep the throttle closed and measure the voltage at TH input. Put the measured value into the field below.
required gain for throttle input | 0.78 |  | result |  | 0.885 | V
required offset for throttle input | 2.57 | V | result | Step 5 | Step 2 - Keep the throttle oppened manually and measure the voltage at TH input. Put the measured value into the field below.
 |  |  |  |  | 4.75 | V
Throttle sensor voltage range | 3.865 | V | calculated |  | Step 3 - Keep the gas pedal not pressed and measure the voltage at GP input. Put the measured value into the field below.
target when closed | 4 | V | constant | Step 6 | 1.2 | V
target when oppened | 1 | V | constant | Step 7 | Step 4 - Keep the gas pedal fully pressed and measure the voltage at GP input. Put the measured value into the field below.
target range | 3 | V | constant |  | 3.5 | V
series diode offset | 0.12 | V | constant |  | Step 5 - using pot PR2 set the voltage in test point B to the below value
 |  |  |  |  | 2.57 | V
 |  |  |  |  | Step 6 - with closed throttle use PR1 to set the voltage at test point A to the below value
Gas pedal |  |  |  |  | 4.00 | V
Gas pedal voltage when not pressed | 1.2 | V | input | Step 3 | Step 7 - open the throttle manually and check voltage at test point A, it should be close to the below value
Gas pedal voltage when fully pressed | 3.5 | V | input | Step 4 | 1.00 | V
 |  |  |  |  | Step 8- using pot PR4 set the voltage in test point D to the below value
required gain for gas pedal input | 1.28 |  | result |  | 2.37 | V
required offset for gas pedal input | 2.37 | V | result | Step 8 | Step 9 - with gas pedal de-pressed use PR3 to set the voltage at test point C to the below value
 |  |  |  |  | 4.00 | V
Gas pedal voltage range | 2.3 | V | calculated |  | Step 10 - press the gas pedal and check voltage at test point C, it should be close to the below value
target when not pressed | 4 | V | constant | Step 9 | 1.05 | V
target when fully pressed | 1.05 | V | constant | Step 10 | Step 11 - Calibration finished, connect the throttle motor and check the behaviour.
target range | 2.95 | V | constant
series diode offset | 0.12 | V | constant |  | Hints:
 |  |  |  |  | - DO NOT connect throttle motor before the calibration is finished!
 |  |  |  |  | - "pot" = "potentiometer"
In case of questions please email: dstagegarage@gmail.com |  |  |  |  | - if you turn pot PR2 all the way up or down and still cannot get the voltage from step 5 you may have to lower the values of R30 and R31
 |  |  |  |  | - if you turn pot PR4 all the way up or down and still cannot get the voltage from step 8 you may have to lower the values of R32 and R33
 |  |  |  |  | - if the throttle is unstable and "flaps" you maymodify the gain of the controller for example by lowering value of R7 and/or increasing R8 (lowers the gain)

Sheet: scratchpad
k | 1.28 |  | out const1 | 4 | V
offset | 2.5 | V | out const2 | 1 | V
 |  |  | rane const | 3 | V
in 1 | 1.2 | V
in 2 | 3.5 | V | in 1 | 3.5 | V
 |  |  | in 2 | 1.2 | V
out 1 | 4.164 | V | in range | 2.3 | V
out 2 | 1.22 | V
 |  |  | K | 1.30
 |  |  | in_1*K | 4.57
 |  |  | in_2*K | 1.57
 |  |  | off_b1 | 0.57
 |  |  | off_b2 | 0.57

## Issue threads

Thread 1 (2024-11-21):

ETC DS 5v

turboedge, 2024-11-21:
If you are trying to align the connections with a DRV8825 then the 5v inputs should be on pins 5-6 not 4-5, though I don't see where they are used for anything, so I suppose it does not matter.

DStageGarage, 2024-11-21:
Yes, you are correct, I missed it but as you said it's not used for anything and shorting pin 4 to 5 and 6 on DSpeed won't hurt either. For a second I was thinking about using this 5V but decided against it to not strain the linear regulator on DSpeed and to perhaps have a less noisy system / better signal integrity.

Closed 2024-11-21.

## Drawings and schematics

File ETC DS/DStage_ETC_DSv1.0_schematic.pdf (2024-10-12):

# DStage ETC DSv1.0 2024.10.05

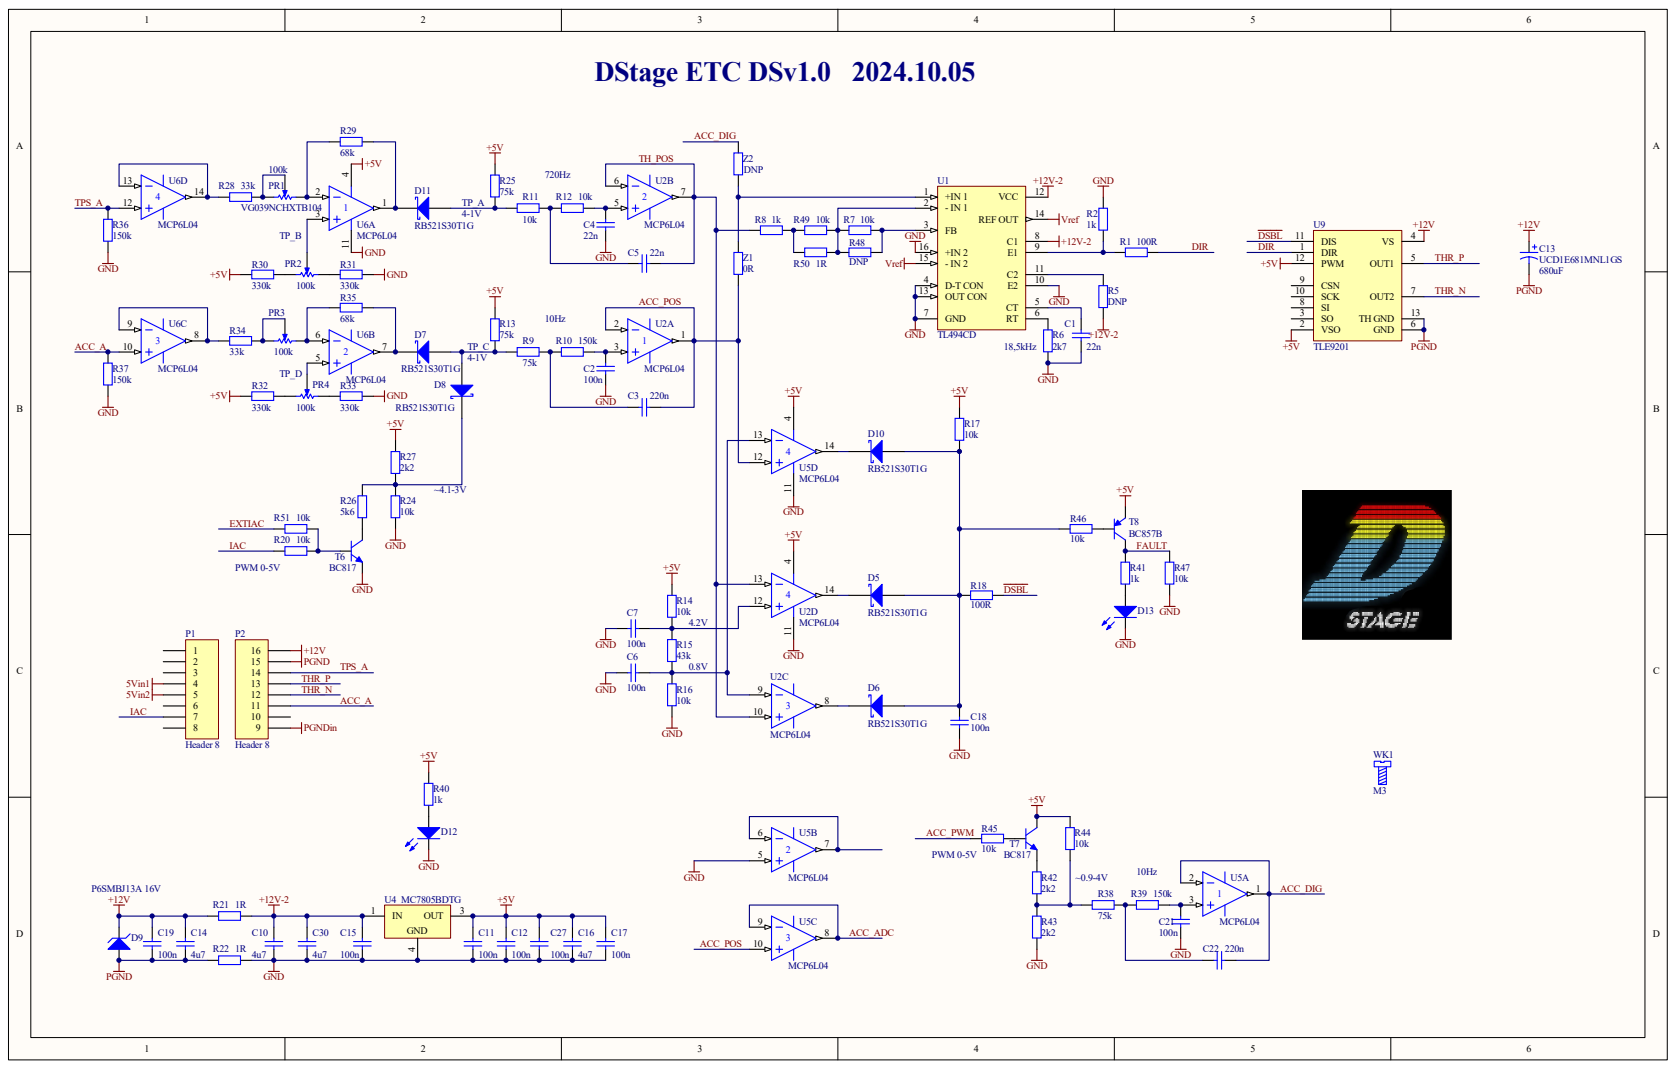
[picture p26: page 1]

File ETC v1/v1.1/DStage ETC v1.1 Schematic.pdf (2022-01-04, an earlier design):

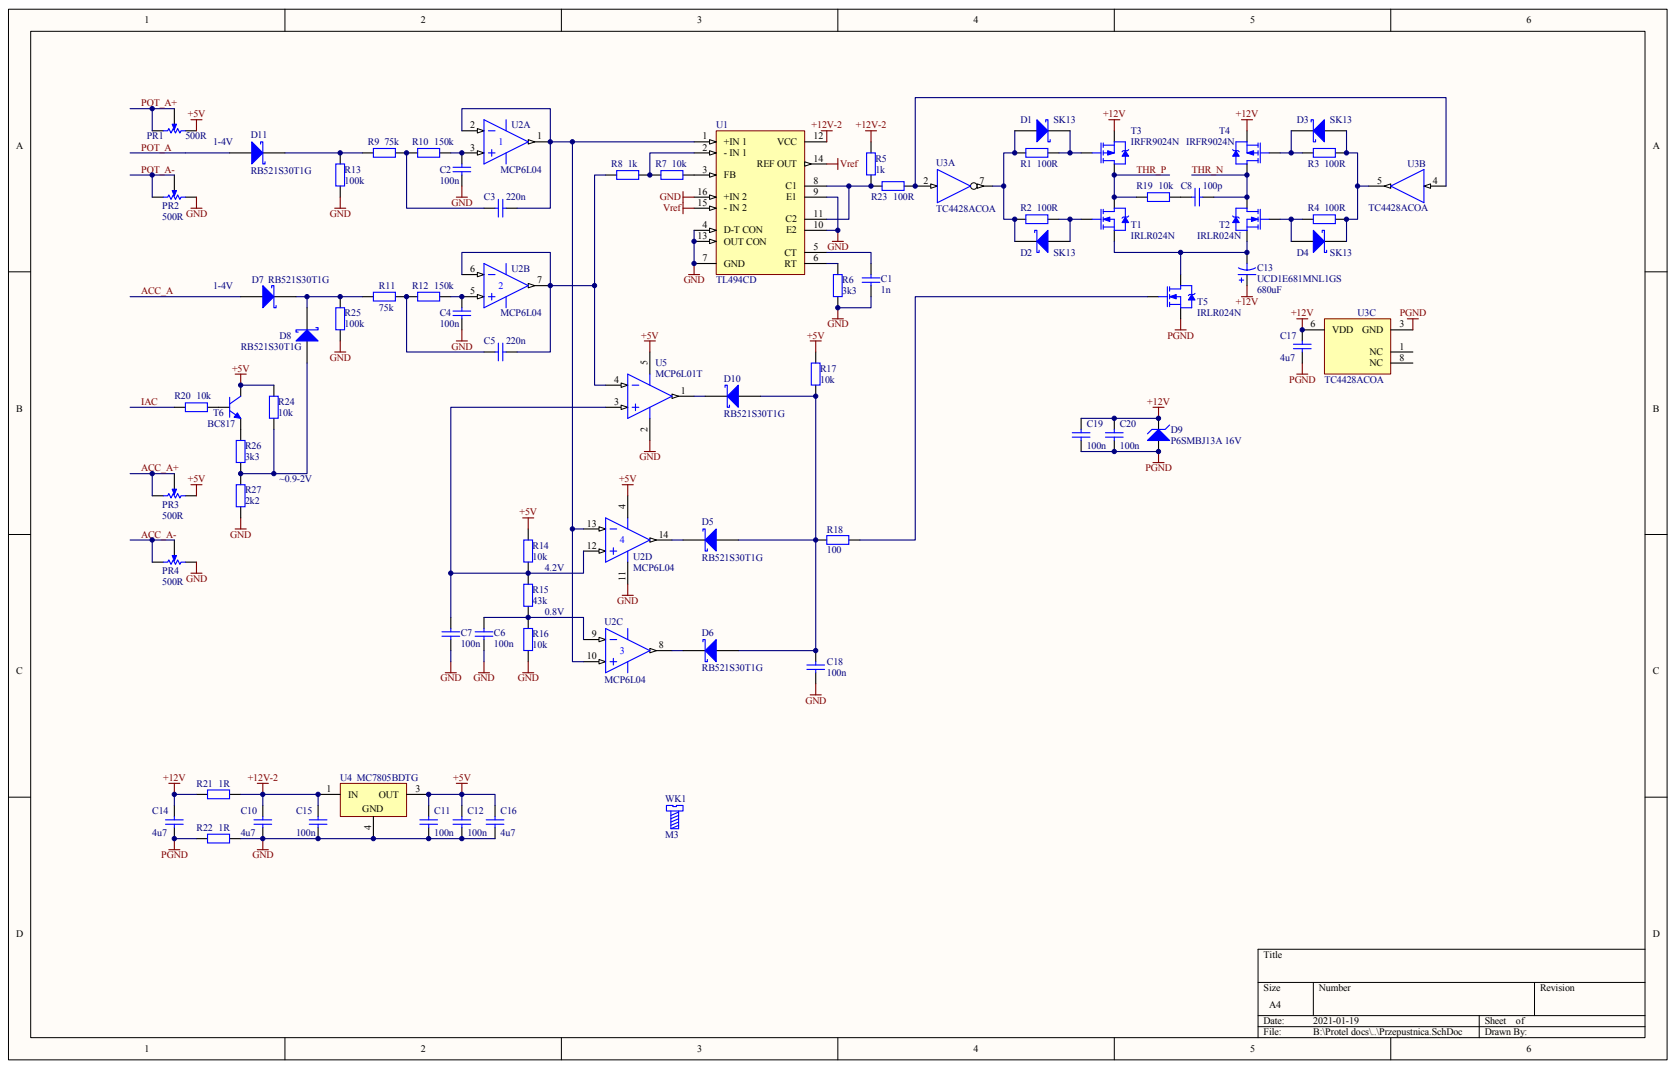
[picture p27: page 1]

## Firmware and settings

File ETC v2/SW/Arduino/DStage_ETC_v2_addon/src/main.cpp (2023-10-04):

#include <Arduino.h>
#include <EEPROM.h>
#include <FreqPeriodCounter.h>

#define led_pin 13

#define TH_ADC A0                                             // analog pin 0 = throttle position input signal
#define ACC_ADC A1                                            // analog pin 1 = gas pedal position input signal
#define FAULT 2                                               // digital pin 2 = fail safe status
#define ACC_PWM 9                                             // digital pin 9 = gas pedal output PWM
#define RPM_IN 3                                              // digital pin 3 = RPM input

#define POS_TAB_SIZE 10                                       // number of position ranges
#define RPM_TAB_SIZE 10                                       // number of RPM ranges (has to be at least 1)
#define POS_TAB_ACT_SIZE (POS_TAB_SIZE+2)                     //
#define RPM_TAB_ACT_SIZE (RPM_TAB_SIZE+2)                     //

#define EE_POS_ADR 0                                          // EEPROM address for position ranges
#define EE_RPM_ADR (EE_POS_ADR + POS_TAB_ACT_SIZE)            // EEPROM address for RMP ranges
#define EE_OUT_ADR (EE_RPM_ADR + RPM_TAB_ACT_SIZE*2)          // EEPROM address for translation table
#define EE_CLOSED_CAL_ADR (EE_OUT_ADR + POS_TAB_ACT_SIZE * RPM_TAB_ACT_SIZE)  // EEPROM addres for gas pedal de-pressed calibration value
#define EE_OPENED_CAL_ADR (EE_CLOSED_CAL_ADR + 2)             // EEPROM addres for gas pedal pressed calibration value

// serial communication aliases
#define COM_FREE 0
#define COM_GET_FULL_T 'F'
#define COM_SEND_FULL_T 'f'
#define COM_GET_RPM_T 'R'
#define COM_SEND_RPM_T 'r'
#define COM_GET_POS_T 'P'
#define COM_SEND_POS_T 'p'
#define COM_EE_BURN 'B'
#define COM_CLOSE_CAL 'C'
#define COM_OPEN_CAL 'O'
#define COM_CAL_BURN 'E'

//uint8_t range_pos[POS_TAB_ACT_SIZE] = {0, 7, 15, 40, 55, 70, 103, 150, 175, 200, 225, 255};
/*uint8_t output_pos[RPM_TAB_ACT_SIZE][POS_TAB_ACT_SIZE] = {
  {0, 10, 25, 50, 75, 120, 110, 75, 50, 25, 10, 255},
  {0, 10, 25, 50, 75, 120, 110, 75, 50, 25, 10, 255},
  {0, 10, 25, 50, 75, 120, 110, 75, 50, 25, 10, 255},
  {0, 10, 25, 50, 75, 120, 110, 75, 50, 25, 10, 255},
  {0, 10, 25, 50, 75, 120, 110, 75, 50, 25, 10, 255},
  {0, 10, 25, 50, 75, 120, 110, 75, 50, 25, 10, 255},
  {0, 10, 25, 50, 75, 120, 110, 75, 50, 25, 10, 255},
  {0, 5, 10, 20, 30, 40, 50, 60, 70, 80, 90, 255},
  {0, 5, 10, 20, 30, 40, 50, 60, 70, 80, 90, 255},
  {0, 5, 10, 20, 30, 40, 50, 60, 70, 80, 90, 255},
  {0, 5, 10, 20, 30, 40, 50, 60, 70, 80, 90, 255},
  {0, 5, 10, 20, 30, 40, 50, 60, 70, 80, 90, 255}};
uint16_t range_rpm[RPM_TAB_ACT_SIZE] = {100, 500, 1000, 2000, 3000, 4000, 5000, 6000, 7000, 8000, 9000, 12000};*/
uint8_t range_pos[POS_TAB_ACT_SIZE];
uint8_t output_pos[RPM_TAB_ACT_SIZE][POS_TAB_ACT_SIZE];
uint16_t range_rpm[RPM_TAB_ACT_SIZE];
uint16_t max_rpm, rpm_temp;
uint8_t command_count=0;
uint8_t command_status=COM_FREE;
uint8_t uni1=0;
uint8_t send_pos_inedx=0, send_rpm_index=0;
float gas_factor=0.4153;
uint16_t closed_calib=205, opened_calib=819;

FreqPeriodCounter counter_ms(RPM_IN, micros);
uint8_t translate_with_weights(uint16_t, uint16_t);
void counterISR();


void setup() 
{
  pinMode(led_pin,OUTPUT);

  // setup output accelerator PWM pin
  pinMode(ACC_PWM, OUTPUT);

  // interrupt for RPM counter
  attachInterrupt(1, counterISR, CHANGE);

  Serial.begin(57600);           //  setup serial

  //EEPROM.put(EE_POS_ADR, range_pos);
  //EEPROM.put(EE_RPM_ADR, range_rpm);
  //EEPROM.put(EE_OUT_ADR, output_pos);

  // read translation table and ranges from EEPROM
  EEPROM.get(EE_POS_ADR, range_pos);
  EEPROM.get(EE_RPM_ADR, range_rpm);
  EEPROM.get(EE_OUT_ADR, output_pos);

  max_rpm = range_rpm[RPM_TAB_ACT_SIZE-1];
 
  // calculate gas calibration factor
  gas_factor = (float)255 / (opened_calib - closed_calib);
}

void loop()
{
  int acc_val;
  int new_out;
  uint8_t ser_data;

  // read input gas pedal position
  acc_val = analogRead(ACC_ADC);

  // calculate new translated position
  // TODO: put measured RPM as second argument
  new_out = translate_with_weights(acc_val, 2000);

  // update stimulus for TL494
  analogWrite(ACC_PWM, new_out);

  if(counter_ms.ready()) 
  {
    // TODO: move "new_out =" here
    // TODO: put in RPM as calculation: 60000/counter_ms.period

  }

  // take care of serial communication inputs
  if(Serial.available())
  {
    ser_data = Serial.read();

    // toggle LED for debug purposes
    if(uni1 == 0)
    {
      digitalWrite(led_pin,HIGH);
      uni1 = 1;
    }
    else
    {
      digitalWrite(led_pin,LOW);
      uni1 = 0;
    }

    // when new command comes
    if(command_status == COM_FREE)
    {
      // receive full translation table
      if(ser_data == COM_GET_FULL_T)
      {
        command_status = COM_GET_FULL_T;
        command_count = POS_TAB_ACT_SIZE * RPM_TAB_ACT_SIZE;
      }

      // receive RPM ranges table
      if(ser_data == COM_GET_RPM_T)
      {
        command_status = COM_GET_RPM_T;
        command_count = RPM_TAB_ACT_SIZE * 2;
      }

      // receive position ranges table
      if(ser_data == COM_GET_POS_T)
      {
        command_status = COM_GET_POS_T;
        command_count = POS_TAB_ACT_SIZE;
      }

      // send full translation table
      if(ser_data == COM_SEND_FULL_T)
      {
        command_status = COM_SEND_FULL_T;
        command_count = POS_TAB_ACT_SIZE * RPM_TAB_ACT_SIZE;
        send_pos_inedx = POS_TAB_ACT_SIZE - 1;
        send_rpm_index = RPM_TAB_ACT_SIZE - 1;
      }

      // send RPM ranges
      if(ser_data == COM_SEND_RPM_T)
      {
        command_status = COM_SEND_RPM_T;
        command_count = RPM_TAB_ACT_SIZE * 2;
      }

      // send position ranges
      if(ser_data == COM_SEND_POS_T)
      {
        command_status = COM_SEND_POS_T;
        command_count = POS_TAB_ACT_SIZE;
      }

      // burn data to EEPROM
      if(ser_data == COM_EE_BURN)
      {
        EEPROM.put(EE_POS_ADR, range_pos);
        EEPROM.put(EE_RPM_ADR, range_rpm);
        EEPROM.put(EE_OUT_ADR, output_pos);

        command_status = COM_FREE;
      }

      // refresh de-pressed gas pedal calibration
      if(ser_data == COM_CLOSE_CAL)
      {
        closed_calib = acc_val;

        command_status = COM_FREE;
      }

      // refresh pressed gas pedal calibration
      if(ser_data == COM_OPEN_CAL)
      {
        opened_calib = acc_val;

        command_status = COM_FREE;
      }

      // store gas pedal calibration in EEPROM
      if(ser_data == COM_CAL_BURN)
      {
        EEPROM.put(EE_CLOSED_CAL_ADR, closed_calib);
        EEPROM.put(EE_OPENED_CAL_ADR, opened_calib);

        command_status = COM_FREE;
      }
    }
    else 
    {
      // receiving full translation table in progress
      if(command_status == COM_GET_FULL_T)                      
      {
        command_count--;                                        // decrease nuber of bytes left to receive

        //uint8_t col, row;
        //col = command_count / RPM_TAB_ACT_SIZE;
        //row = command_count % RPM_TAB_ACT_SIZE;
        //output_pos[col][row] = ser_data;                       // save new data

        uint8_t *tab_point = &output_pos[0][0];
        *(tab_point + command_count) = ser_data;                // save new data from the end

        // when last byte of the command received
        if(command_count == 0)
          command_status = COM_FREE;
      }

      // receiving RPM ranges table in progress
      if(command_status == COM_GET_RPM_T)                      
      {
        uint8_t temp_index;

        command_count--;
  
        if ((command_count & 0x01) == 0)
        {
            // odd bytes = MSB
            rpm_temp = rpm_temp + (((uint16_t)ser_data) << 8);

            temp_index = command_count >> 1;
            range_rpm[temp_index] = rpm_temp;
        }
        else
        {
            // even bytes = LSB
            rpm_temp = ser_data;
        }

        // when last byte of the command received
        if(command_count == 0)
          command_status = COM_FREE;
      }

      // receiving position ranges table in progress
      if(command_status == COM_GET_POS_T)                      
      {
        command_count--;                                        // decrease nuber of bytes left to receive

        range_pos[command_count] = ser_data;

        // when last byte of the command received
        if(command_count == 0)
          command_status = COM_FREE;
      }
    }
  } 

  // handling commands sending data back to PC
  // send back full translation table
  if((command_status == COM_SEND_FULL_T))// && (Serial.availableForWrite()))
  {
    delay(12);

    Serial.write(output_pos[send_rpm_index][send_pos_inedx]);

    if(send_pos_inedx == 0)
    {
      send_pos_inedx = POS_TAB_ACT_SIZE - 1;
      send_rpm_index--;
    }
    else
      send_pos_inedx--;

    command_count--;                                          // decrease nuber of bytes left to send

    //uint8_t *tab_point = &output_pos[0][0];
    //Serial.write(*(tab_point + command_count));             // send new data from the end

    //when last byte of the command send
    if(command_count == 0)
    {
      command_status = COM_FREE;
      delay(12);
    }
  }

  // send RPM ranges table
  if(command_status == COM_SEND_RPM_T)
  {
    uint8_t temp_index;

    command_count -= 2;
    temp_index = command_count >> 1;

    // send LSB and MSB
    Serial.write((uint8_t)(range_rpm[temp_index] & 0xFF));
    delay(12);
    Serial.write((uint8_t)(range_rpm[temp_index] >> 8));
    delay(12);

    //when last byte of the command send
    if(command_count == 0)
    {
      command_status = COM_FREE;
      delay(12);
    }
  }

  // send position ranges table
  if(command_status == COM_SEND_POS_T)
  {
    command_count--;                                          // decrease nuber of bytes left to send

    delay(12);
    Serial.write(range_pos[command_count]);

    //when last byte of the command send
    if(command_count == 0)
    {
      command_status = COM_FREE;
      delay(12);
    }
  }

}


// interrupt for RPM counter
void counterISR()
{ 
  counter_ms.poll();
}

// based on input position and RPM read values from translation table and aproximate the output from up to 4 points
uint8_t translate_with_weights(uint16_t input_pos, uint16_t input_rpm)
{
  uint8_t i1, pos1, pos2, in_pos;
  unsigned int rpm1, rpm2, dif1, dif2, dif_tot, in_temp;
  float weip1, weip2, weir1, weir2, output;

  // normalize input position to calibrated gas pedal range
  if(input_pos < closed_calib)
    input_pos = closed_calib;  
  in_temp = (float)(input_pos - closed_calib) * gas_factor;
  if(in_temp > 255)
    in_temp = 255;
  in_pos = in_temp;

  // RPM - find points and calculate weights (assuming top limit cannot be exceeded)
  for(i1=1;i1<RPM_TAB_ACT_SIZE;i1++)                          // sweep through RPM ranges
  {
    if(input_rpm <= range_rpm[i1])                            // when range found
    {
        dif_tot = range_rpm[i1] - range_rpm[i1-1];
        dif1 = input_rpm - range_rpm[i1-1];
        dif2 = range_rpm[i1] - input_rpm;

        weir1 = (float)dif2 / dif_tot;
        weir2 = (float)dif1 / dif_tot;

        rpm1 = i1 - 1;
        rpm2 = i1;
        
      i1 = RPM_TAB_ACT_SIZE;                                  // exit for loop
    }
  }

  // POSITION - find points and calculate weights
  for(i1=1;i1<POS_TAB_ACT_SIZE;i1++)            
  {
    if(in_pos < range_pos[i1])                             // when range found
    {
        dif_tot = range_pos[i1] - range_pos[i1-1];
        dif1 = in_pos - range_pos[i1-1];
        dif2 = range_pos[i1] - in_pos;

        weip1 = (float)dif2 / dif_tot;
        weip2 = (float)dif1 / dif_tot;

        pos1 = i1 - 1;
        pos2 = i1;
 
        i1 = POS_TAB_ACT_SIZE;                                // exit for loop
    }
  }

  // calculate translated position acording to 4 points with weights
  output = (float)(((float)output_pos[rpm1][pos1] * weip1) + ((float)output_pos[rpm1][pos2] * weip2)) * weir1;
  output += (float)(((float)output_pos[rpm2][pos1] * weip1) + ((float)output_pos[rpm2][pos2] * weip2)) * weir2;

  return (uint8_t)output;
}

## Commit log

2022-01-04 Added gerbers for version 1.2
2022-01-04 Link to BOM added
2022-05-08 Updated BOM, manual and PCB
    PCB v1.3 allows for embedding the project into custom ECU as now all signal and power pads have a hole for placing standard goldpin. BOM was updated with corrected TPS input filter values. Manual includes basic calibration procedure and short instruction for ordering the boards from JLCPCB.
    [DStage_ETC_v1.3_BOM.xlsx]
2022-05-10 Corrected pick and place format
    [DStage_ETC_v1.3_PnP.csv]
2023-03-26 Updated BOM and schematic in manual
    [DStage_ETC_v1.3_BOM.xlsx]
2023-07-27 New generation board v2.2 aded
    New generation v2.x and new version v2.2 now available.
    [DStage_ETC_v2.2_BOM.xlsx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]
2023-07-27 Calibration spreadsheet added
    [DStage_ETC_v2.2_calibration.xlsx]
2023-07-28 Correction of calibration sheet
    Formula had "+" instead of "-"
    [DStage_ETC_v2.2_calibration.xlsx]
2023-08-22 Alternative version of BOM including connectors
    [DStage_ETC_v2.2_with_connectors_BOM.xlsx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]
2023-08-29 Model for case 3d print
    [DStage ETC v2.x case basic project.f3d, DStage ETC v2.x case lid no holes.stl, DStage ETC v2.x case main no holes.stl]
2023-08-29 case for ETC v2.x basic image
2023-08-29 image for basic case
2023-08-30 Alternative case for v2.x by RSMtuning
    [DStage_ETC_v2.x_case_by_RSMtuning.f3d, DStage_ETC_v2.x_case_by_RSMtuning_lid.stl, DStage_ETC_v2.x_case_by_RSMtuning_main.stl]
2023-09-06 3d model of case for v1.x
    [DStage ETC v1.x case basic project.f3d, DStage ETC v1.x case lid no holes.stl, DStage ETC v1.x case main no holes.stl]
2023-10-02 Changed repo layout, readme updated
    [DStage ETC v1.x case basic project.f3d, DStage ETC v1.x case lid no holes.stl, DStage ETC v1.x case main no holes.stl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]
2023-10-04 Arduino beta code added for v2.2
2024-06-17 added schematic for v2.2
2024-07-21 Calibration procedure sheet now has more details
    [DStage_ETC_v2.2_calibration.xlsx]
2024-07-21 Calibration sheet has more details and hints
    [DStage_ETC_v2.2_calibration.xlsx]
2024-08-11 Typos corrected in calibration procedure
    [DStage_ETC_v2.2_calibration.xlsx]
2024-10-12 Production files added
    [DStage_ETC_DSv1.0_BOM.xlsx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]
2024-10-12 added schematic and PCB render
2024-11-13 low gain variant BOM added
    [DStage_ETC_v2.2_BOM_low_gain.xlsx, DStage_ETC_v2.2_with_connectors_BOM_low_gain.xlsx]
2024-11-13 low gain BOM added
    [DStage_ETC_v1.3_BOM_low_gain.xlsx]
